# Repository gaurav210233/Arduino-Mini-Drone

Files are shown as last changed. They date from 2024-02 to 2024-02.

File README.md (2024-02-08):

# Arduino-Mini-Drone

## Breakout Boards
* Arduino Pro Mini ATMEGA328P 5V/16M - https://robu.in/product/atmega328p-pro-mini-5v-16mhz-compatible-with-arduino/
* GY-91 MPU9250+BMP280 10DOF Acceleration Gyro 9-Axis Sensor Module - https://robu.in/product/gy-91-mpu9250bmp280-10dof-acceleration-gyro-9-axis-sensor-module/
* M177 NRF24L01 2.4GHz Antenna Wireless Transceiver Module - https://robu.in/product/m177-nrf24l01-2-4ghz-antenna-wireless-transceiver-module/

## Libraries
* Bolder Flight Systems MPU9250 - https://github.com/bolderflight/invensense-imu
* Adafruit_BMP280_Library - https://github.com/adafruit/Adafruit_BMP280_Library
* RF24 - https://github.com/nRF24/RF24

## Useful Links
* Interactive BOM V2 - https://gaurav210233.github.io/Arduino-Mini-Drone/Arduino-Mini-Drone-KiCad/V2/bom/ibom.html
* Interactive BOM V2-ESC - https://gaurav210233.github.io/Arduino-Mini-Drone/Arduino-Mini-Drone-KiCad/V2-ESC/bom/ibom.html
* Interactive BOM V2-FC - https://gaurav210233.github.io/Arduino-Mini-Drone/Arduino-Mini-Drone-KiCad/V2-FC/bom/ibom.html

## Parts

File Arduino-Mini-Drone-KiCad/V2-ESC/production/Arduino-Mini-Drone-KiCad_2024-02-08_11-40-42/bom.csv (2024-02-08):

Designator | Footprint | Quantity | Value | LCSC Part #
B+ | JST_PH_B2B-PH-K_1x02_P2.00mm_Vertical | 1 | PWR
C10, C11, C12, C13 | 0805 | 4 | 22uf | C109447
C14, C15 | CP_EIA-3528-12_Kemet-T_Pad1.50x2.35mm_HandSolder | 2 | 100uf | C171664
C17 | 0603 | 1 | 10uf | C380316
C18, C19 | 0603 | 2 | 100nf | C14663
D3, D4, D5, D6 | D_MELF_Handsoldering | 4 | SS34 | C3011102
D9 | LED_WS2812B_PLCC4_5.0x5.0mm_P3.2mm | 1 | WS2812B | C2761795
H5, H6, H7, H8 | MountingHole_2.2mm_M2_Pad_Via | 4 | MountingHole
M1 | PinHeader_1x02_P1.27mm_Vertical | 1 | Motor1
M2 | PinHeader_1x02_P1.27mm_Vertical | 1 | Motor2
M3 | PinHeader_1x02_P1.27mm_Vertical | 1 | Motor3
M4 | PinHeader_1x02_P1.27mm_Vertical | 1 | Motor4
NEO | PinHeader_1x08_P1.27mm_Vertical | 1 | POWER
NEO_Enable | SolderJumper-2_P1.3mm_Open_Pad1.0x1.5mm | 1 | LED ON OFF
Q1, Q2, Q3, Q4 | SOT-23 | 4 | AO3400A | C347475
Q5 | SOT-23 | 1 | AO3401A | C347476
R10, R4, R6, R8 | 0603 | 4 | 10k | C25804
R11, R5, R7, R9 | 0603 | 4 | 100 | C19702
R12 | 0603 | 1 | 100k | C25803
R13 | 0603 | 1 | 33k | C4216
R14 | 0603 | 1 | 390 | C23151

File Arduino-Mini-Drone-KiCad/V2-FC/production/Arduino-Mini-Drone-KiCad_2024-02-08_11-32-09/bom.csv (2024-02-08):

Designator | Footprint | Quantity | Value | LCSC Part #
BZ1 | PinHeader_1x02_P1.27mm_Vertical | 1 | Buzzer
C1, C2, C3, C6 | 0603 | 4 | 0.1uf | C71629
C4, C5 | CP_EIA-3216-10_Kemet-I_Pad1.58x1.35mm_HandSolder | 2 | 10uf | C600516
C7, C8 | 0603 | 2 | 1uf | C15849
C9 | 1206 | 1 | 10uf | C600516
D1 | 0603 | 1 | Green | C241891
D2 | 0603 | 1 | Red | C266784
H1, H2, H3, H4 | MountingHole_2.2mm_M2_Pad_Via | 4 | MountingHole
J1 | PinHeader_1x08_P1.27mm_Vertical | 1 | NRF24
J11 | PinHeader_1x03_P1.27mm_Vertical | 1 | PPM
J13 | PinHeader_1x05_P1.27mm_Vertical | 1 | Open
J2 | PinHeader_1x06_P1.27mm_Vertical | 1 | UART + BT
J7 | PinHeader_1x08_P1.27mm_Vertical | 1 | MCU
R1, R3 | 0603 | 2 | 10K | C25804
R2 | 0603 | 1 | 330 | C23140
U1 | TQFP-32_7x7mm_P0.8mm | 1 | ATmega328P-A | C14877
U2 | SOT-23-5_HandSoldering | 1 | MIC5205YM5 | C412820
U3 | SOT-23-5_HandSoldering | 1 | LP5907MFX-3.3 | C5370990
VCC | PinSocket_1x05_P2.54mm_Vertical | 1 | MPU9250 + BMP280
Y1 | Crystal_SMD_5032-4Pin_5.0x3.2mm | 1 | Crystal_GND2 | C124318

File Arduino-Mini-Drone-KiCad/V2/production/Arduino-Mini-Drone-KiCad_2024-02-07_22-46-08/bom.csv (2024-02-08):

Designator | Footprint | Quantity | Value | LCSC Part #
B+, B+1 | JST_PH_B2B-PH-K_1x02_P2.00mm_Vertical | 2 | PWR
BZ1, BZ2 | PinHeader_1x02_P1.27mm_Vertical | 2 | Buzzer
C1, C16, C2, C20, C21, C24, C3, C6 | 0603 | 8 | 0.1uf | C71629
C10, C11, C12, C13, C28, C29, C30, C31 | 0805 | 8 | 22uf | C109447
C14, C15, C32, C33 | CP_EIA-3528-12_Kemet-T_Pad1.50x2.35mm_HandSolder | 4 | 100uf | C171664
C17, C34 | 0603 | 2 | 10uf | C380316
C18, C19, C35, C36 | 0603 | 4 | 100nf | C14663
C22, C23, C4, C5 | CP_EIA-3216-10_Kemet-I_Pad1.58x1.35mm_HandSolder | 4 | 10uf | C600516
C25, C26, C7, C8 | 0603 | 4 | 1uf | C15849
C27, C9 | 1206 | 2 | 10uf | C600516
D1, D7 | 0603 | 2 | Green | C241891
D10, D11, D12, D13, D3, D4, D5, D6 | D_MELF_Handsoldering | 8 | SS34 | C3011102
D14, D9 | LED_WS2812B_PLCC4_5.0x5.0mm_P3.2mm | 2 | WS2812B | C2761795
D2, D8 | 0603 | 2 | Red | C266784
H1, H10, H11, H12, H13, H14, H15, H16, H2, H3, H4, H5, H6, H7, H8, H9 | MountingHole_2.2mm_M2_Pad_Via | 16 | MountingHole
J1, J3 | PinHeader_1x08_P1.27mm_Vertical | 2 | NRF24
J11, J12 | PinHeader_1x03_P1.27mm_Vertical | 2 | PPM
J13, J14 | PinHeader_1x05_P1.27mm_Vertical | 2 | Open
J2, J4 | PinHeader_1x06_P1.27mm_Vertical | 2 | UART + BT
J7, J8 | PinHeader_1x08_P1.27mm_Vertical | 2 | MCU
M1, M5 | PinHeader_1x02_P1.27mm_Vertical | 2 | Motor1
M2, M6 | PinHeader_1x02_P1.27mm_Vertical | 2 | Motor2
M3, M7 | PinHeader_1x02_P1.27mm_Vertical | 2 | Motor3
M4, M8 | PinHeader_1x02_P1.27mm_Vertical | 2 | Motor4
NEO, NEO1 | PinHeader_1x08_P1.27mm_Vertical | 2 | POWER
NEO_Enable, NEO_Enable1 | SolderJumper-2_P1.3mm_Open_Pad1.0x1.5mm | 2 | LED ON OFF
Q1, Q2, Q3, Q4, Q6, Q7, Q8, Q9 | SOT-23 | 8 | AO3400A | C347475
Q10, Q5 | SOT-23 | 2 | AO3401A | C347476
R1, R10, R15, R17, R18, R20, R22, R24, R3, R4, R6, R8 | 0603 | 12 | 10K | C25804
R11, R19, R21, R23, R25, R5, R7, R9 | 0603 | 8 | 100 | C19702
R12, R26 | 0603 | 2 | 100k | C25803
R13, R27 | 0603 | 2 | 33k | C4216
R14, R28 | 0603 | 2 | 390 | C23151
R16, R2 | 0603 | 2 | 330 | C23140
U1, U4 | TQFP-32_7x7mm_P0.8mm | 2 | ATmega328P-A | C14877
U2, U5 | SOT-23-5_HandSoldering | 2 | MIC5205YM5 | C412820
U3, U6 | SOT-23-5_HandSoldering | 2 | LP5907MFX-3.3 | C5370990
VCC, VCC1 | PinSocket_1x05_P2.54mm_Vertical | 2 | MPU9250 + BMP280
Y1, Y2 | Crystal_SMD_5032-4Pin_5.0x3.2mm | 2 | Crystal_GND2 | C124318
mouse-bite-2mm-slot_2, mouse-bite-2mm-slot, mouse-bite-2mm-slot1_6, mouse-bite-2mm-slot1_5, mouse-bite-2mm-slot1_4, mouse-bite-2mm-slot1_3, mouse-bite-2mm-slot1_2, mouse-bite-2mm-slot1 | mouse-bite-2mm-slot | 8 | VAL**

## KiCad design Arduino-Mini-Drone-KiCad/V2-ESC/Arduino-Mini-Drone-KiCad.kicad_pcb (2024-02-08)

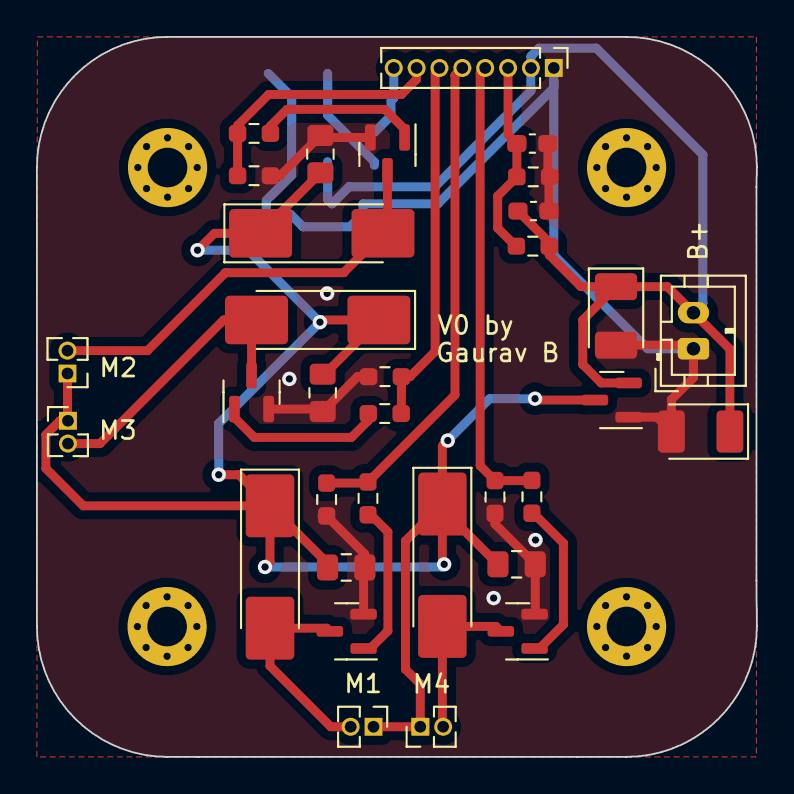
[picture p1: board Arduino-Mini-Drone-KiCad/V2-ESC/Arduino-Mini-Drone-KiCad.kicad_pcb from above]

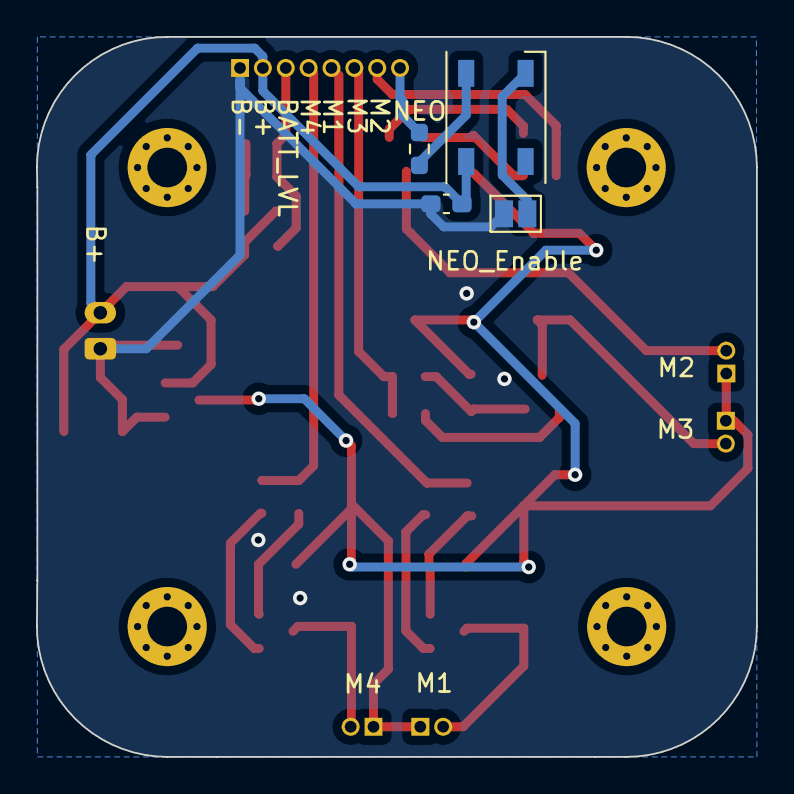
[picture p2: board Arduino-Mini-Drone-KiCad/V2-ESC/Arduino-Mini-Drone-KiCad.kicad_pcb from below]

Board: 2 copper layers, 40.0 x 40.0 mm, 41 parts (4 on the bottom side), 19 nets.

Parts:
B+: PWR; JST_PH_B2B-PH-K_1x02_P2.00mm_Vertical
C10, C11, C12, C13: 22uf; C_0805_2012Metric_Pad1.18x1.45mm_HandSolder
C14, C15: 100uf; CP_EIA-3528-12_Kemet-T_Pad1.50x2.35mm_HandSolder
C17: 10uf; C_0603_1608Metric_Pad1.08x0.95mm_HandSolder
C18, C19: 100nf; C_0603_1608Metric_Pad1.08x0.95mm_HandSolder
D3, D4, D5, D6: SS34; D_MELF_Handsoldering
D9: WS2812B; LED_WS2812B_PLCC4_5.0x5.0mm_P3.2mm
H5, H6, H7, H8: MountingHole; MountingHole_2.2mm_M2_Pad_Via
M1: Motor1; PinHeader_1x02_P1.27mm_Vertical
M2: Motor2; PinHeader_1x02_P1.27mm_Vertical
M3: Motor3; PinHeader_1x02_P1.27mm_Vertical
M4: Motor4; PinHeader_1x02_P1.27mm_Vertical
NEO: POWER; PinHeader_1x08_P1.27mm_Vertical
NEO_Enable: LED ON OFF; SolderJumper-2_P1.3mm_Open_Pad1.0x1.5mm
Q1, Q2, Q3, Q4: AO3400A; SOT-23
Q5: AO3401A; SOT-23
R4, R6, R8, R10: 10k; R_0603_1608Metric_Pad0.98x0.95mm_HandSolder
R5, R7, R9, R11: 100; R_0603_1608Metric_Pad0.98x0.95mm_HandSolder
R12: 100k; R_0603_1608Metric_Pad0.98x0.95mm_HandSolder
R13: 33k; R_0603_1608Metric_Pad0.98x0.95mm_HandSolder
R14: 390; R_0603_1608Metric_Pad0.98x0.95mm_HandSolder

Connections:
+BATT: B+.2, C14.1, C15.1, C17.2, C19.2, D9.1 (VDD), NEO.2, Q5.2 (S), R12.1
-BATT: B+.1, C10.1, C11.1, C12.1, C13.1, C14.2, C15.2, C17.1, C18.1, C19.1, NEO.1, NEO_Enable.2 (B), Q1.2 (S), Q2.2 (S), Q3.2 (S), Q4.2 (S), Q5.1 (G), R4.1, R6.1, R8.1, R10.1, R13.2
BATT LVL: C18.2, NEO.3, R12.2, R13.1
D4 IN: NEO.8, R14.1
M1: NEO.5, R4.2, R5.2
M2: NEO.7, R6.2, R7.2
M3: NEO.6, R8.2, R9.2
M4: NEO.4, R10.2, R11.2
unnamed: D3.2 (A), M1.2, Q1.3 (D)
unnamed: D4.2 (A), M2.2, Q2.3 (D)
unnamed: D5.2 (A), M3.2, Q3.3 (D)
unnamed: D6.2 (A), M4.2, Q4.3 (D)
unnamed: D9.4 (DIN), R14.2
unnamed: D9.3 (VSS), NEO_Enable.1 (A)
unnamed: Q1.1 (G), R5.1
unnamed: Q2.1 (G), R7.1
unnamed: Q3.1 (G), R9.1
unnamed: Q4.1 (G), R11.1
VMOT: C10.2, C11.2, C12.2, C13.2, D3.1 (K), D4.1 (K), D5.1 (K), D6.1 (K), M1.1, M2.1, M3.1, M4.1, Q5.3 (D)

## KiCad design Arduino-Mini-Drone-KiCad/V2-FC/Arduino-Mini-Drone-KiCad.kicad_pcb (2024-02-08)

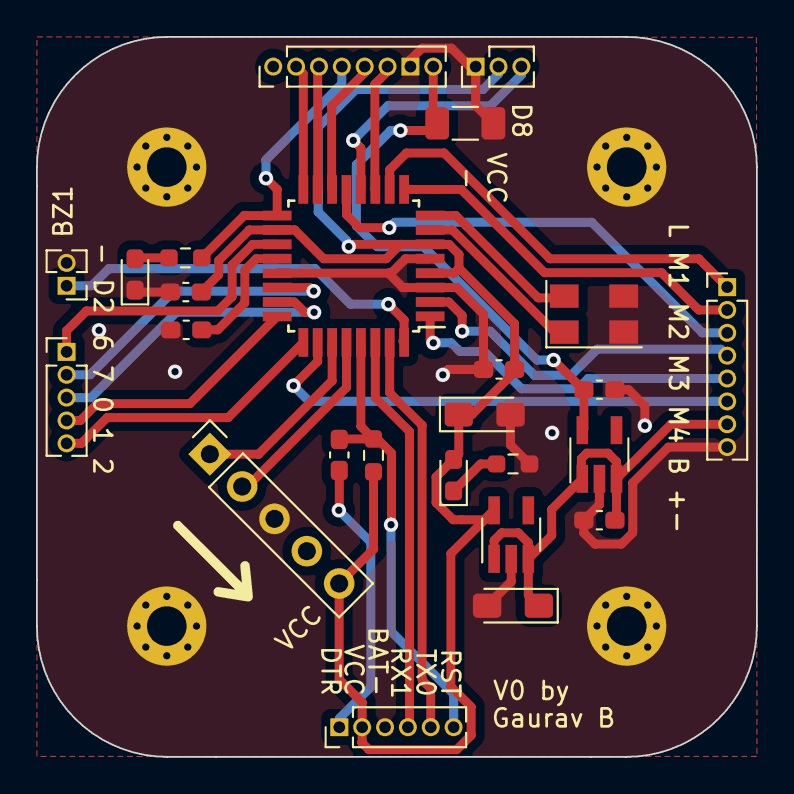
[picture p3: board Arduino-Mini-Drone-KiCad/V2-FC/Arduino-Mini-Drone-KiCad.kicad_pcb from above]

Board: 2 copper layers, 40.0 x 40.0 mm, 29 parts (0 on the bottom side), 33 nets.

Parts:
BZ1: Buzzer; PinHeader_1x02_P1.27mm_Vertical
C1, C2, C3, C6: 0.1uf; C_0603_1608Metric_Pad1.08x0.95mm_HandSolder
C4, C5: 10uf; CP_EIA-3216-10_Kemet-I_Pad1.58x1.35mm_HandSolder
C7, C8: 1uf; C_0603_1608Metric_Pad1.08x0.95mm_HandSolder
C9: 10uf; C_1206_3216Metric_Pad1.33x1.80mm_HandSolder
D1: Green; LED_0603_1608Metric_Pad1.05x0.95mm_HandSolder
D2: Red; LED_0603_1608Metric_Pad1.05x0.95mm_HandSolder
H1, H2, H3, H4: MountingHole; MountingHole_2.2mm_M2_Pad_Via
J1: NRF24; PinHeader_1x08_P1.27mm_Vertical
J2: UART + BT; PinHeader_1x06_P1.27mm_Vertical
J7: MCU; PinHeader_1x08_P1.27mm_Vertical
J11: PPM; PinHeader_1x03_P1.27mm_Vertical
J13: Open; PinHeader_1x05_P1.27mm_Vertical
R1: 10K; R_0603_1608Metric_Pad0.98x0.95mm_HandSolder
R2: 330; R_0603_1608Metric_Pad0.98x0.95mm_HandSolder
R3: 10k; R_0603_1608Metric_Pad0.98x0.95mm_HandSolder
U1: ATmega328P-A; TQFP-32_7x7mm_P0.8mm
U2: MIC5205YM5; SOT-23-5_HandSoldering
U3: LP5907MFX-3.3; SOT-23-5_HandSoldering
VCC: MPU9250 + BMP280; PinSocket_1x05_P2.54mm_Vertical
Y1: Crystal_GND2; Crystal_SMD_5032-4Pin_5.0x3.2mm

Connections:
+3.3V: C8.2, C9.1, J1.8, U3.5 (OUT)
+BATT IN: C4.1, C7.2, J7.7, U2.1 (IN), U2.3 (EN), U3.1 (IN), U3.3 (EN)
-BATT: BZ1.2 (-), C2.1, C3.1, C4.2, C5.2, C6.1, C7.1, C8.1, C9.2, D1.1 (K), H1.1, H2.1, H3.1, H4.1, J1.7, J2.3, J7.8, J11.1, R3.1, U1.3 (GND), U1.5 (GND), U1.21 (GND), U2.2 (GND), U3.2 (GND), VCC.3, Y1.2, Y1.3
A0: J13.3, U1.23 (PC0)
A1: J13.4, U1.24 (PC1)
A2: J13.5, U1.25 (PC2)
A3: J7.6, U1.26 (PC3)
A4: U1.27 (PC4), VCC.1
A5: U1.28 (PC5), VCC.2
A6: J13.1, U1.19 (ADC6)
A7: J13.2, U1.22 (ADC7)
D2: BZ1.1 (+), U1.32 (PD2)
D3: J7.5, U1.1 (PD3)
D4: J7.4, U1.2 (PD4)
D5: J7.2, U1.9 (PD5)
D6: J7.1, U1.10 (PD6)
D7: J1.6, U1.11 (PD7)
D8: J11.3, U1.12 (PB0)
D9: J7.3, U1.13 (PB1)
D10: J1.5, U1.14 (PB2)
D11: J1.3, U1.15 (PB3)
D12: J1.2, U1.16 (PB4)
D13: J1.4, R2.2, U1.17 (PB5)
DTR: C1.2, J2.1
unnamed: D1.2 (A), R2.1
unnamed: D2.1 (K), R3.2
unnamed: C2.2, U1.20 (AREF)
unnamed: U1.7 (XTAL1/PB6), Y1.1
unnamed: U1.8 (XTAL2/PB7), Y1.4
RST: C1.1, J2.6, R1.1, U1.29 (~RESET/PC6)
RX1: J2.4, U1.30 (PD0)
TX0: J2.5, U1.31 (PD1)
VCC: C3.2, C5.1, C6.2, D2.2 (A), J2.2, J11.2, R1.2, U1.4 (VCC), U1.6 (VCC), U1.18 (AVCC), U2.5 (OUT), VCC.5

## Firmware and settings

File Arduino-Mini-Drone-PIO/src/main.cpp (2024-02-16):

#define TEST_ENABLED 0

#if TEST_ENABLED
  #define TEST_NRF24_ENABLED 1
  #define TEST_MPU9250_ENABLED 1
  // #define TEST_CMOTORS_ENABLED 0
#endif


#include <Arduino.h>
#include "custom_nrf24.h"
#include "custom_mpu9250.h"

CustomNrf24 nrf;

void setup()
{
  Serial.begin(115200);
  #if TEST_ENABLED
    #if TEST_NRF24_ENABLED
      nrf.begin();
    #endif
  #endif 
}

void loop()
{
  #if TEST_ENABLED
    test();
  #endif
}

#if TEST_ENABLED
  void test()
  {
    #if TEST_NRF24_ENABLED
      testNrf24();
    #endif

    #if TEST_MPU9250_ENABLED

    #endif
  }
#endif

#if TEST_NRF24_ENABLED
  void testNrf24()
  {
    nrf.receive();
    nrf.printData();
    delay(100); // Adjust delay as needed
  }
#endif

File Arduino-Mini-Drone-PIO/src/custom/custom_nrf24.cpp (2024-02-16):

#include "custom_nrf24.h"

CustomNrf24::CustomNrf24() : drone_radio(CE, CSN) {}

void CustomNrf24::dataReset()
{
    data.Joy1_X = 512;
    data.Joy1_Y = 512;
    data.Joy2_X = 512;
    data.Joy2_Y = 512;
    data.Joy1_SW = 1;
    data.Joy2_SW = 1;
    data.Toggle1_SW =1;
    data.Toggle2_SW =1;
    data.SW_A = 1;
    data.SW_B = 1;
    data.SW_C = 1;
    data.SW_D = 1;
    data.Pot1 = 0;
    data.Pot2 = 0;
    data.degX = 0;
    data.degY = 0;
}

void CustomNrf24::begin()
{
    drone_radio.begin();
    drone_radio.openReadingPipe(0, address);
    drone_radio.setPALevel(RF24_PA_MIN);
    drone_radio.startListening();
    dataReset();
}

void CustomNrf24::receive()
{
    // check if there is received data
    if(drone_radio.available())
    {
        drone_radio.read(&data, sizeof(stick_position));
        lastReceivedTime = millis();
    }

    // Disconnected if more than 1 second since last data received.
    // Move all switch positions to neutral
    currentReceptionTime = millis();
    if( currentReceptionTime - lastReceivedTime > 1000)
    {
        dataReset();
    }
}

void CustomNrf24::printData()
{
    // Show all switch positions on serial monitor
    Serial.print("Joy1-X: ");
    Serial.print(data.Joy1_X);
    Serial.print(" Joy1-Y: ");
    Serial.print(data.Joy1_Y);
    Serial.print(" Joy2-X: ");
    Serial.print(data.Joy2_X);
    Serial.print(" Joy2-Y: ");
    Serial.print(data.Joy2_Y);
    Serial.print(" Joy1_SW: ");
    Serial.print(data.Joy1_SW);
    Serial.print(" Joy2_SW: ");
    Serial.print(data.Joy2_SW);
    Serial.print(" Pot1: ");
    Serial.print(data.Pot1);
    Serial.print(" Pot2: ");
    Serial.print(data.Pot2);
    Serial.print(" Toggle1: ");
    Serial.print(data.Toggle1_SW);
    Serial.print(" Toggle2: ");
    Serial.print(data.Toggle2_SW);
    Serial.print(" SW_A: ");
    Serial.print(data.SW_A);
    Serial.print(" SW_B: ");
    Serial.print(data.SW_B);
    Serial.print(" SW_C: ");
    Serial.print(data.SW_C);
    Serial.print(" SW_D: ");
    Serial.print(data.SW_D);
    Serial.print(" X_angle: ");
    Serial.print(data.degX);
    Serial.print(" Y_angle: ");
    Serial.println(data.degY);
}

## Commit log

2024-01-11 added some breakout boards to readme
2024-01-11 installed imu and altitude library
2024-01-17 Added wrapper functions * To initialize bmp * To get - Altitude, Pressure, Temperature Added Comments from original library
2024-01-17 Added functions to initialize IMU and calibrate magnetometer
2024-01-17 added functions to read the IMU
2024-01-17 created KiCad files, completed schematics, downloaded Datasheets
    [Arduino-Mini-Drone-KiCad.kicad_pcb, Arduino-Mini-Drone-KiCad.kicad_sch]
2024-01-22 added mpu9250 lib & completed PCB layout
    [Arduino-Mini-Drone-KiCad.kicad_pcb, Arduino-Mini-Drone-KiCad.kicad_sch]
2024-01-22 created copy for easy components
    [Arduino-Mini-Drone-KiCad.kicad_pcb, Arduino-Mini-Drone-KiCad.kicad_sch]
2024-02-06 Completed Panelized PCB in V2 delete Row 2 PCB for error resolution
    [Arduino-Mini-Drone-KiCad.kicad_pcb, Arduino-Mini-Drone-KiCad.kicad_sch]
2024-02-06 added interactive BOM
2024-02-06 Added link to Readme for BOM
2024-02-08 Created Seperate boards for ESC and FC
    [Arduino-Mini-Drone-KiCad.kicad_pcb, Arduino-Mini-Drone-KiCad.kicad_sch, bom.csv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]
2024-02-08 Restructured Folders
    [Arduino-Mini-Drone-KiCad.kicad_pcb, Arduino-Mini-Drone-KiCad.kicad_sch, bom.csv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]
2024-02-08 Added BOM
